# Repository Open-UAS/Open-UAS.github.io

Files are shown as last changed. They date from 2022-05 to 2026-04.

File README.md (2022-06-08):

# [OpenUAS Documentation](https://open-uas.github.io/)

This repository hosts the documentation as a VuePress site. The content can be edited by modifying the .md files and committing the changes.
When pushed to master the website will be recompiled and deployed to https://open-uas.github.io/

See [here](https://open-uas.github.io/Meta_Docs) for details on contributing to this documentation.

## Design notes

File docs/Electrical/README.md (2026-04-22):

# Electrical

Here, you will find details on the electrical system on the current OpenUAS vehicle, including wiring diagrams, recommended components, and device pin-outs.

## Apprentice, 3.0 Wiring Diagram, and 5.0 Wiring Diagram
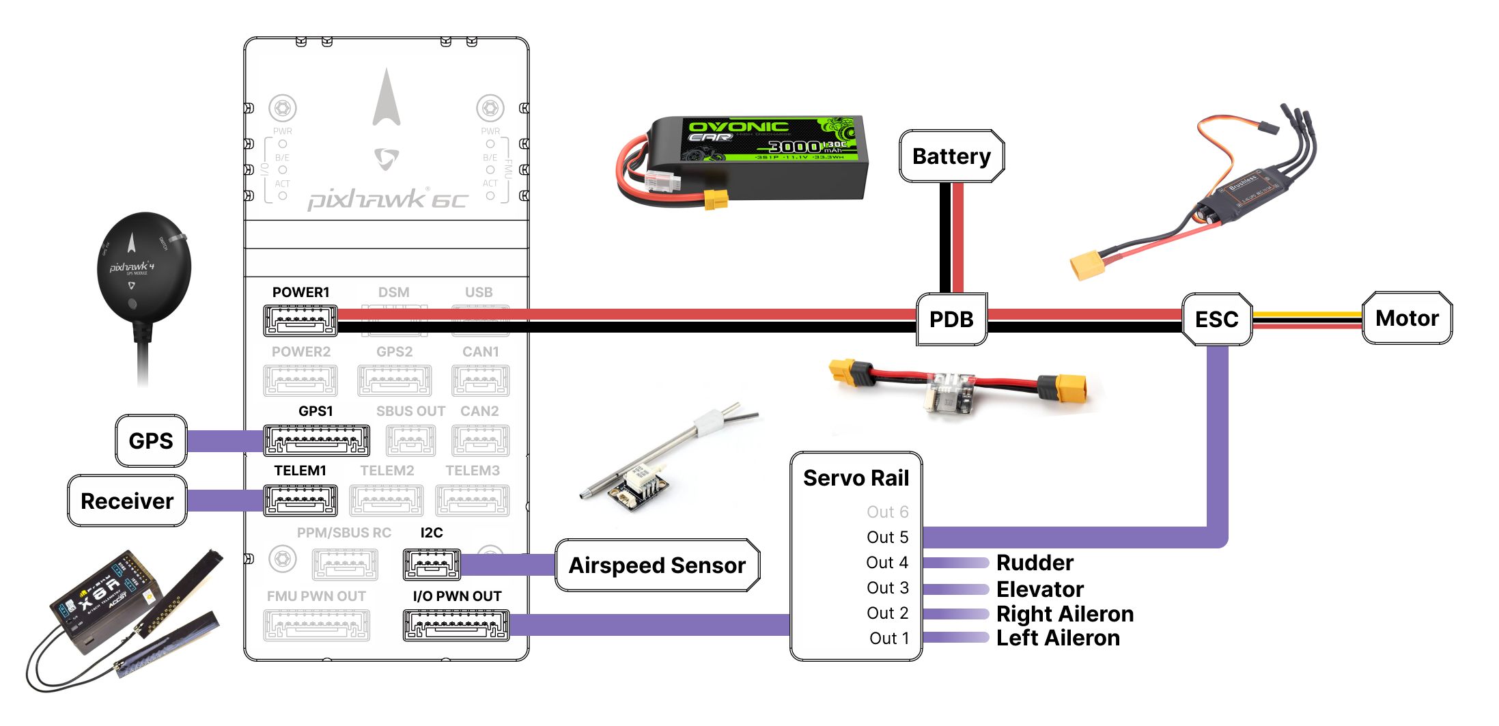
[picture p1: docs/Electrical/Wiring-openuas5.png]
Wiring Diagram Current
 

## PLUMA Wiring Diagram
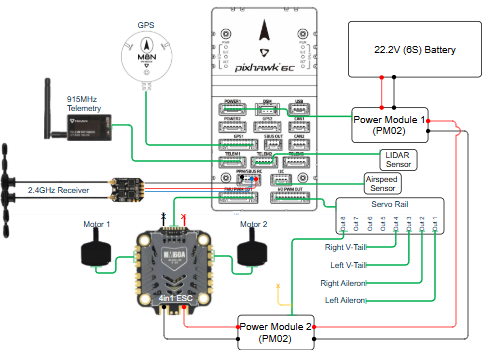
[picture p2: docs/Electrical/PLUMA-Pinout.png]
Wiring Diagram


## Pixhawk 4 Pinout
[Pixhawk 4 Pinout](/Pixhawk4-Pinouts.pdf)
## testing

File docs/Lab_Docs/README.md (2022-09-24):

# Lab Docs
Here you will find general documentation about using tools in the lab or other general documentation.

[iMAX B6 V2 battery charger manual](/manual-iMAXB6AC-v2.pdf)

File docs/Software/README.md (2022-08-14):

# Software

The software solution utilized can be broken up into a few major sections.
* [PX4](PX4.md) Onboard firmware that controls the vehicle and performs autonomous actions.
* [QGroundControl](QGroundControl.md) Ground control software that receives telemetry information commands actions.
* [Simulation](Simulation.md) Software to simulation flight dynamics, used in testing and training.

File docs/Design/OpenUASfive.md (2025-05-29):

# Open UAS 5.0 (work in prog-Karan)
## Summary
The main objective of the OpenUAS 5.0 model is to be affordable and simplistic in materials. The model is designed to serve as a kit with a set of detailed instructions. The 5.0 model is made of a fully 3D printed airframe allowing for more complex geometry with improved aerodynamics The instructions for this model breaks down each step with details, tips, and visuals to aid the reader's process of assembling the model (Still Under Development).

## Goals
- Cost-effective
- Reconfigurable
- Easy to manufacture
- Optimized for research payloads
- 3D printed airframe

## Project Progress:
## CFD Analysis
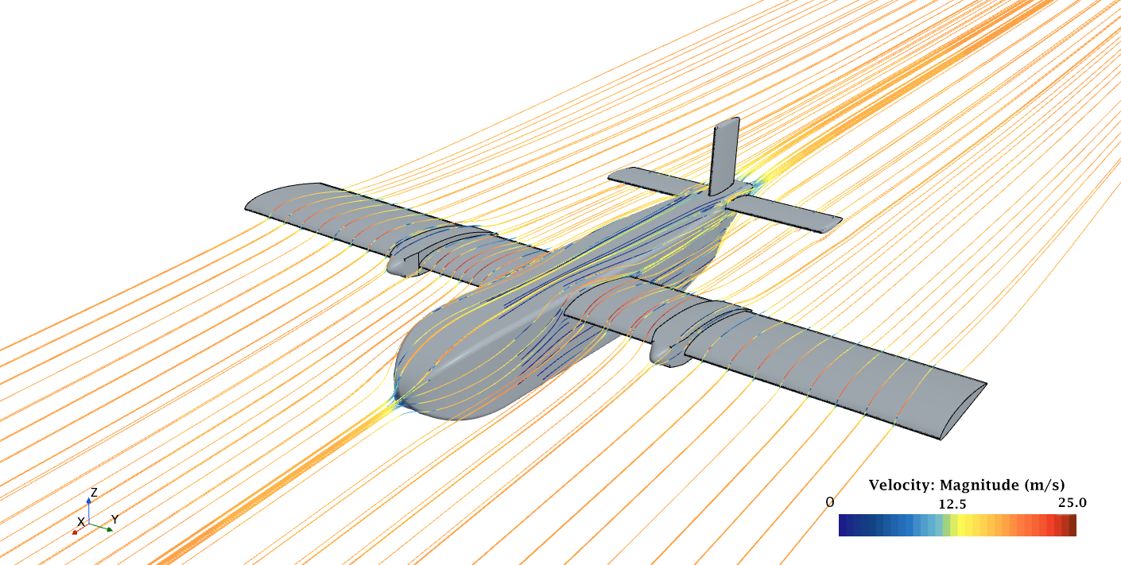
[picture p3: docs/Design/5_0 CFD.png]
OpenUAS 5.0 initial CFD


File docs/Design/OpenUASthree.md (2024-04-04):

# Open UAS 3.0 
## Summary
The main objective of the OpenUAS 3.0 model is to be affordable and simplistic in materials. The model is designed to serve as a kit with a set of detailed instructions. The 3.0 model is largely composed of posterboard and 3D printed materials. The instructions for this model breaks down each step with details, tips, and visuals to aid the reader's process of assembling the model.

## Goals
- Lightweight
- Cost-effective
- Reconfigurable
- Easy to manufacture
- Optimized for electronics

## Solidworks Assembly
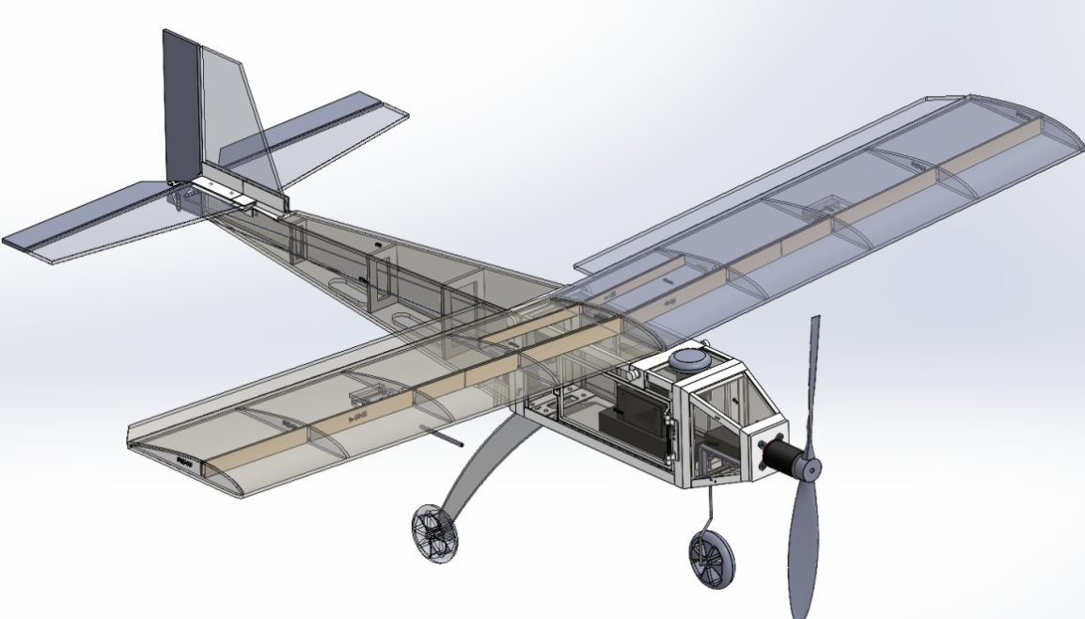
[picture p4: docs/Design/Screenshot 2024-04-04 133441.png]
OpenUAS 3.0 Solidworks


## Model
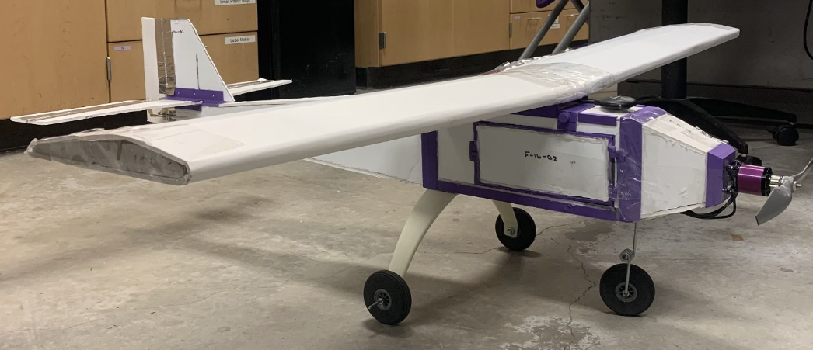
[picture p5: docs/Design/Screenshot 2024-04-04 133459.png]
OpenUAS 3.0 Completed


### Spring 2023 Updates
With this design, we optimized the NACA 2412 airfoil to create the desired aerodynamic characteristics for the wing. By modifying the original NACA 2412, we increased lift and drag slightly.

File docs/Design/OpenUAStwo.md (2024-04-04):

# Open UAS 2.0 
## Summary  
The OpenUAS 2.0 model has a major focus on the use of 3D printed parts to create a framework that can be easily modfided and printed to meet the needs for anyone wanting to use the model. It has an overall weight of 4.07 lbs, keeping it lightweight. It is also adaptable to store more electronics than OpenUAS 1.0 and other UAVs. 

## Requirements: 
- Lightweight
- Cost-effective
- Easy to manufacture
- Optimized for electronics
- Stable during flight

## Solidworks Assembly
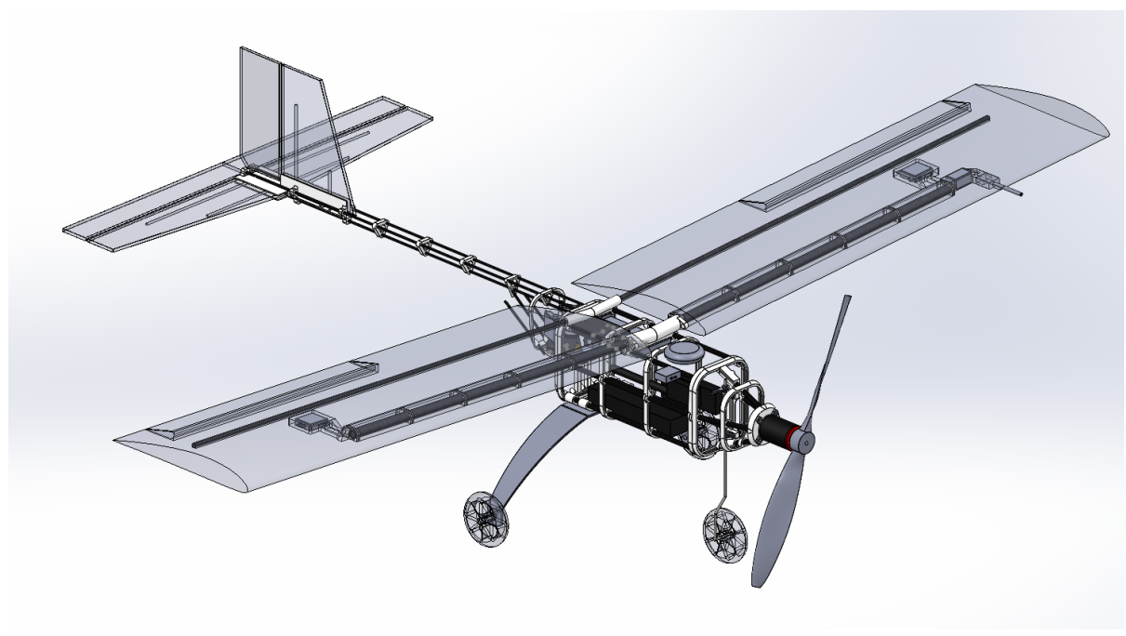
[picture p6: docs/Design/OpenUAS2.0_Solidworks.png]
Solidworks complete


## Model
OpenUAS 2.0 Completed

We will go through some design changes made from Jan 2022-May 2023.

## Spring 2022 Design Changes

There were a few issues that arose with the construction of the 2nd iteration of the OpenUAS project. These were mostly forecasted issues the team had planned mitigation methods for, but  that ended up not working the intended way. There were a few issues that arose that were not foreseen but directly related to the predicted issues. 

## The First Major Area of Issue 
The issues we were faced with all revolved around the tail of the UAS. The original idea was to create a tail that's lightweight and easily replaceable. In order to do this the tail was broken down into a few different parts. These included the carbon fiber support rod, and 3D printed parts including: tail supports, tail feather support, and connection rod of the tail.  

### Twisting of the tail 
The first issue that arose was the amount of twist that appeared in the end of the tail around the tail feather piece. We predicted that there would be a small amount of twist due to using 3 Carbon Fibers rods as the main part of the tail. We believed that it would be negligible, however once the tail was assembled it was clear the twisting was going to be more of an issue then originally predicted.  

One way we attempted to fix this issue was adding more of the tail support pieces in order to add more stiffness along the carbon fiber rods. While this did decrease the amount of twist noticeably, it still did not remove the problem. Other proposed ideas for fixing for the issue was adding a stiffer such as balsa wood or popsicle sticks was taken into consideration however, while working to find a solution the team ran into another issue. 

### Connection between the body and the tail 

Another issue we ran into was not one that we had predicted. When designing the 3D pieces the team created generic ribs that would be used to create the body of the UAS. There were a few assumptions made however when applying the concept of the hinge ribs with the interfacing parts such as the back connection point and the nose cone connection. 

One of the assumptions made was that the 3D printed parts would be printed to a high enough tolerance that connecting with glue while flush with each other would be a quick and easy method of connecting and if needed later removing from each other without having to completely disassemble the body or tail parts. This proved to not be the case when the time came to connect the two parts. 

One thing that had been overlooked with the 3D printed parts was the flexibility of the pieces. ABS was the material used to print the ribs and the connection piece and while the material considered relatively stiff for our needs the material is still able to bend or warp without losing its shape if a force applied to it. When we went to attach the parts together, we clamped the two of them together; it became hard to hold them together while the glue set and the final product was not within the desired tolerance of connection. Instead of a solid connection we had half of the connection bowing outwards towards the end of the tail instead of inwards toward the body like we had planned. 

The issue was made worse when the control surfaces were added to the tail feather and it was clear the added weight was making the problem worse. Much like the twisting problem we had a number of proposed ideas in order to correct the issue. Looking at table 1.

### Table 1
Solution | How it would fix the problem | Why we went with it or not | Was it the final solution we picked? |
|:----:|:---------------------------------------------------------------|:--------------------------------------------------------------------------|:---------:|
| Elastic bands | The elastic bands would be fastened to the top of the tail piece and then would be wrapped and unwrapped around a part connected to the body of the UAS when accessing the electronics. | After creating a mock-up setup of the idea using string we determined that the flexibility of the ABS material was keeping us from properly tensioning the string and would not be a great solution to the issue. | No |
| Velcro | The top surface of the body and the tail connection piece are meant to be flush when assembled. In order to keep the tail piece from bowing backwards velcro would be placed along the top of the back rib and the connection tailpiece. When we need access to the electronics and interior of the UAS the top piece of velcro would be removed in order to allow the hinge to work correctly. | When we tested the idea by placing velcro pieces on the surface it was seen that the bowing still occurred. Not only that but when moving the UAS the velcro came loose and was not effective.  | No |
| Rod method 1 | This method would include attaching another carbon fiber rod at the base of the body and the end of the tail feather diagonally to force the tail piece upwards. | This method would have been hard to add to the current design as is and runs the risk of breaking during rough landings. | No |
| Rod method 2 | Similar to the 1st rod method the 2nd would involve adding a new rod. A big difference in the method would be removing the 3 smaller carbon fiber rods and replacing them with one large rod that would run from the nose cone to the end of the tail.Instead of adding the diagonal support from the body to the tail. | Like the first rod method we would have to re-design the 3D printed parts. In this case we decided that this approach would be effective in fixing the issue in the smallest amount of time and amount of labor. It would also result in fixing the issue with the twist of the tail feather. | Yes |

## Our solution to the First Issue 
After mocking up and reviewing different ideas between the sub-teams we determined that using the 2nd rod method would be our best course of action. This was based on the fact the rod would not only fix the issue with the bowing but it would also address the twisting problem in the tail at the same time. 

We were not able to mock up this idea in our lab space however, we were able to compare the stiffness from the assembled tail and the singular rod we would add. We did this by applying a small amount of force on each of the structures to determine how much bending would occur. (should we measure the amount of bending for quantitative data(plus another table would be cool))
Once we determined that the singular rod would be the best solution to reduce the bowing in the part we took a look at the twisting. In order to incorporate the rod we had to redesign the tail feather and connection parts. Our theory is that by taking the time to redesign the tail feather we can reduce the twisting at the end of the tail. Primary because the bowing and bending of the 3 carbon fiber rods will no longer be a problem when the tail is one solid rod along the length of the UAS’s body and tail.

## Second Area of Issue 

After the assmebly of the new tail was completed we came across another issue with the 2.0 model. The issue this time instead of being around the tail was the on the body/fuselogde of the model. This model includes the use of neodynimum magnets inorder to keep the clam shell design closed during however, it was discovered that the smaller magnets were not strong enough to hold the shell closed under minor turbulance. 

### Table 2 
Solution | How it would fix the problem | Why we went with it or not | Was it the final solution we picked? |
|:----:|:---------------------------------------------------------------|:--------------------------------------------------------------------------|:---------:|
| Velcro| The Velcro would be able to hold the two halfs closed during flight| We chose not to go with this soultion as there was not enough surface area for the velcro to be affective. | No |
| Zip Ties | Zip Ties is somthing we chose to use as a short term solution in order to close the clam shell | long term the soultion this is not sustanble as the zip ties would have to be cut and a new one to replace them each time we wanted access to the electronics | No |
| 3D Printed Part | A 3D printed part would be more of an insert piece that would screwed together in order to keep the two halfs closed | This was our chosen soultion as it would not add a lot to the system and would a good fit for the part | Yes |

# Spring 2023 Changes 

The changes made during this round were needed for fine tuning of components for the function of the model instead of fixing dramic issues with model like previous changes.  

## Motor Mount Adjustment

After some observions of other air crafts we noticed that the motors for the propeller may benfit from an angled motor instead of a completly straight faceing. We angled our motor to the right and directed down of the model. In order to do this we added nuts to the motor bolts to create the spacing for the angle. This inculded four mounting points and a total of 5 nuts. Two of the nuts were placed on the upper right corner and the upper left corner. 

## Test Flight
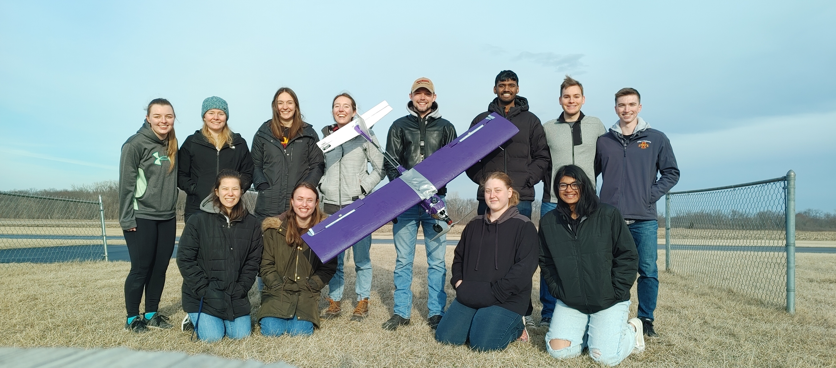
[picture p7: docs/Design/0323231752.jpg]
OpenUAS 2.0 Flight Test


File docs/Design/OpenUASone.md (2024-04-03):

# Open UAS 1.0 

A carbon fiber edtion of the OpenUAS project, built in 2020.
#
OpenUAS1.0 Full Design

More information can be found on the [Laboratory for Temporal Logic Youtube Page](https://www.youtube.com/watch?v=xZF81fSSzbI).
### Requirements include:

1. Configurable: Wings can be changed
2. Can break down and moved easily
3. Simple assembly
4. Does not require a runway
5. Can be manufactured by hobbyist
6. Can withstand a crash landing

### Design Goals
Development for design goals began in 2019.

Overall weight: 4.138 lbs

### Lessons Learned
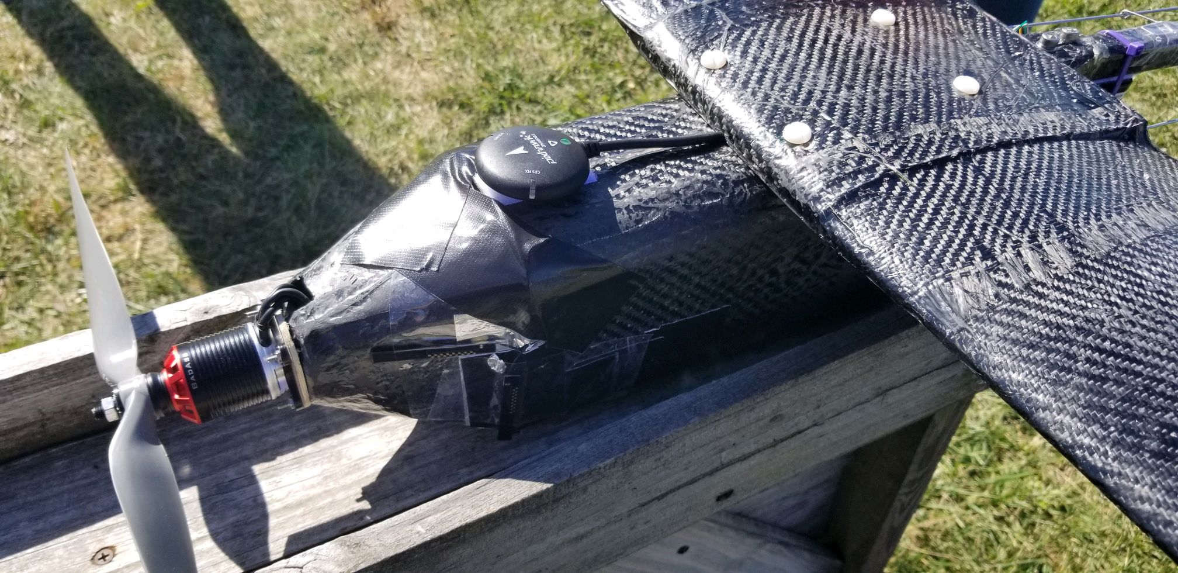
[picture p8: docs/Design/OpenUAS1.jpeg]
OpenUAS 1.0 Completed
\
The next iteration must have the following capabilities:
- Better access to electronics
- Better flight characteristics
- Better reparability
- Tailwheel configuration is harder to control
- Better Manufacturability
- Better transportability (multiple piece wing)
- Better corrective action for left turning tendencies

### Team 
Team Members from left to right: Will Burken, John Edgren, Ellie Diersen, Marcella Anderson, Colton Glick, John Levandowski (not pictured), Christopher Johannsen (not pictured), Stephanie Jou (not pictured)
#
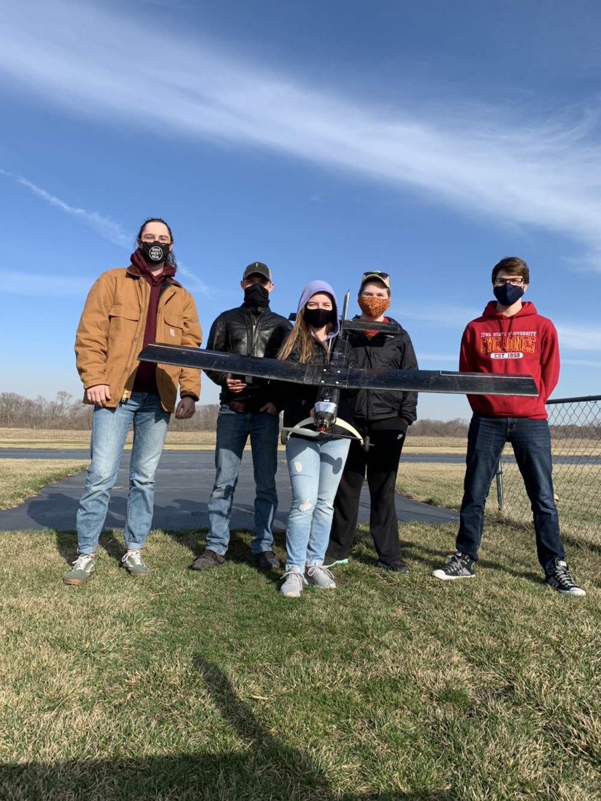
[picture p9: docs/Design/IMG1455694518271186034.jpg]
OpenUAS 1.0 Team


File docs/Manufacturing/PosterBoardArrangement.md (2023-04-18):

# Poster Board Arrangement Settings  
Poster boards can be used to manufacture some parts of the fuselage and wing. It's important to find the best arrangement of these parts to reduce material waste. This problem is generally referred to as the bin packing problem. Several algorithms have been developed to solve this problem before with JS, MATLAB, and C++. Based on our research, the libnest2d library is the easiest, most effective algorithm for finding the best arrangement to cut parts on the poster board. To ease the process, PrusaSlicer 2.5.0 can be downloaded since the libnest2d library is already integrated within this open-source 3D printing software.  
 
References:<br> 
[Bin Packing Problem](https://en.wikipedia.org/wiki/Bin_packing_problem)<br>
[Libnest2d Library](https://github.com/tamasmeszaros/libnest2d)<br>
[PrusaSlicer Download](https://www.prusa3d.com/page/prusaslicer_424/)
 
## 1. Create STL Files 
First, to use the PursaSlicer, you will need to create STL files of your parts using CAD software such as Fusion360 or SolidWorks. If you are using Fusion360, you can export the parts as STL files by right-clicking on the body and selecting 'Save as Mesh'. Even if your parts are designed in other units, you must choose the mm units from the 'Save as Mesh' options. If you are using SolidWorks, you can go to File -> Save As and select the document type as STL. Then, click on the 'Options' button and convert the units to mm. PrusaSlicer software doesn't have the option to change the global units. If STL files are exported with inch units, you can scale the parts by 2540%. It's important to note that the thickness of your parts must be the same as the thickness of the material that will be used.  
 
## 2. Import to PrusaSlicer 
After opening the PrusaSlicer, set the bed dimensions to the same size as your material board in mm units from Printer Settings -> Bed Shape -> Settings -> Size. Then head back to the Plater page, and you can import as many parts as possible  
from File -> Import or using the Ctrl + I shortcut. 
 
## 3. Arrange (Bin Packing Problem) 
The imported parts can be in different orientations. Rotate each part until they are all parallel to the bed. Select the required spacing between parts and check to enable the rotations option by right-clicking on the arrange option at the toolbox bar on the upper side of the window. Then you can check for different alignment options with shortcut A. If you are cutting the parts with CNC for better machining, make sure the spacing is at least the same as the tolerance of your machine. If you are cutting the parts with a knife, we recommend setting the spacing to 1 mm.   
 
## 4.1 Export (For Machining) 
If your machine works with G-code, you can easily export the G-code with Ctrl + G shortcut. If STEP, DWG, or DXF formats are needed, we recommend exporting the plate as an STL file and then post-processing it in Fusion360 or SolidWorks with relevant manufacturing settings. 
 
## 4.2 Export (For Cutting with Knife) 
 
<u>1. via Fusion360</u>
 
After exporting the plate as an STL file, open it via Fusion360. Go to  
Design Workspace -> Mesh -> Modify -> Convert Mesh and select all the meshes to convert them to bodies. Now, you can see the coordinates of your parts on the bottom right of the window by clicking on the corner points of the parts. If the origin is not the same as the bed origin in PrusaSlicer, go to Manufacture Workspace -> Fabrication -> Setup. Set operation type as cutting and orientation as select X & Y axes. Select the X and Y axis from the corner of the reference region manually (Red: x-axis / Green: y-axis) and then set the origin setting to the selected point. 
 
<u>2. via SolidWorks</u>

Go to File -> Open and select the STL file. Then, click on the 'Options' button and select the surface body from the 'import as' option. You can see the coordinates of your parts on the bottom right of the window by clicking on the corner points of the parts.  
 
You can mark these locations on the posterboard and connect the dots to create the part drawings to cut them with a utility knife. We recommend holding a metal straight edge flush with the edge you are cutting and running the knife along the metal.  

Here is the poster board arrangement (22x28-in) we created following the procedures above.

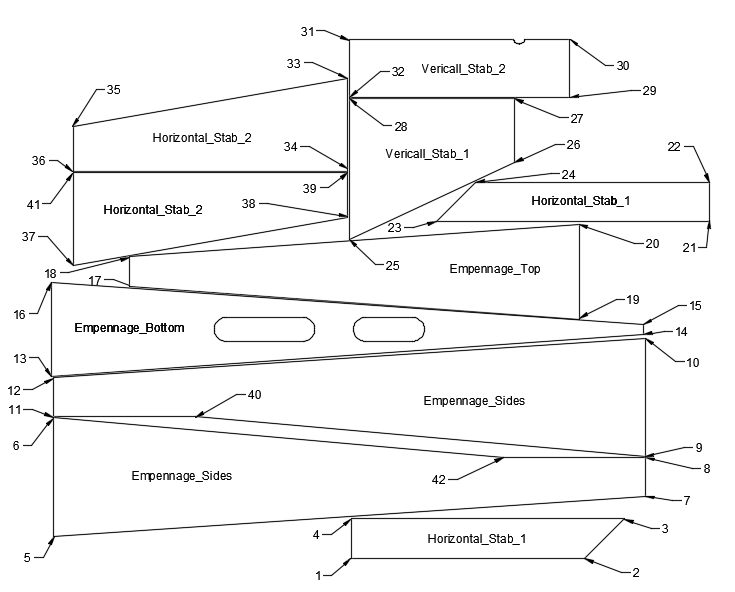
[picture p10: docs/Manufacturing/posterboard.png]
Poster Board


| # | x-axis | y-axis | # | x-axis | y-axis | # | x-axis | y-axis | # | x-axis | y-axis |
|---|---|---|---|---|---|---|---|---|---|---|---|
| 1 | 323.848  | 0.254 | 12 | 4.561 | 194.502  | 23 | 415.121  | 361.505  | 34 | 320.514 | 415.991 |
| 2 | 574.673  | 0.254 | 13 | 2.497 | 195.357  | 24 | 457.624  | 404.008  | 35 | 25.747 | 463.784 |
| 3 | 617.176  | 42.757 | 14 | 637.497  | 241.077  | 25 | 322.022  | 342.299  | 36 | 25.747 | 415.991 |
| 4 | 323.848  | 42.757 | 15 | 637.497  | 251.237  | 26 | 499.314  | 424.971  | 37 | 25.747 | 314.709 |
| 5 | 4.651 | 24.167 | 16 | 2.497 | 296.957  | 27 | 499.314  | 494.046  | 38 | 320.514 | 366.69 |
| 6 | 4.651 | 151.167  | 17 | 86.038 | 291.945  | 28 | 322.022  | 494.046  | 39 | 320.514 | 414.483 |
| 7 | 639.561  | 66.5 | 18 | 86.038 | 324.05 | 29 | 558.75 | 495.3 | 40 | 156.961 | 152.169 |
| 8 | 639.561  | 108.833  | 19 | 568.638  | 257.197  | 30 | 558.75 | 557.213  | 41 | 25.747 | 414.483 |
| 9 | 639.561  | 109.835  | 20 | 568.638  | 358.798  | 31 | 321.768  | 557.213  | 42 | 487.161 | 108.833 |
| 10 | 639.561  | 236.835  | 21 | 708.449  | 361.505  | 32 | 321.768  | 495.3 | 43 | | |
| 11 | 4.561 | 152.169  | 22 | 708.449  | 404.008  | 33 | 320.514  | 515.764  | 44 | | |

X and Y coordinates are in mm units.

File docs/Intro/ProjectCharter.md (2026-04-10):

# Project Charter

## Project Name
OpenUAS

## Principal Investigator
Dr. Kristin Y. Rozier

## Project Team
- Artur Nunes
- Mukul Kulkarni
- Broderick Urbanz
- Grant Goebel
- Tyler Kazmarski
- Gustavo Luzzi
- Sam McClure
- Grace Gilsdorf
- Aidan Sippel
- Karanvir Singh
- Akwasi Quarcoo
- Saira Farooz
- Anderson Keough
- Abhigyaan Deep 
- Maria Zambrano Sanchez
- Fionna Schaack
- Shersta Anupindi

## Revisions
* **Revision:** E
* **Rev Date:** 05/26/2025
* **Originally Dated:** 09/20/2017

## Background
No open-source UAS options exist that are fixed-wing and accessible (conceptually) to the general public. Some similar, available UAS’ are the Albatross (created and sold commercially by Applied Aeronautics) and Razor (created a UVA). Open source software options already available include ArduPilot and PX4.

## Project Scope
We are producing an open-source, COTS UAS that can be used for education and research purposes; the UAS shall only consist of components available to the general public. 

## Project Objectives
* Create an open-source, COTS UAS for educational and research flights
* Provide full documentation of the conception, design, and testing of all systems
* Act as a test bed for Dr. Rozier's system health management experiments
* Be easily launched and not require a runway for takeoff or landing
* Be piloted by students and hobbyists
* Be reconfigurable and support additional components

## Project Deliverables
* A functioning design and prototype of a UAS
* Relevant tools for piloting the UAS from the ground
* Extensive documentation of the design process
* Extensive documentation of the manufacturing process
* Extensive documentation on proper use and safety

## Project Constraints
* COTS components
* Affordable components
* Easily duplicated components (e.g. all 3D printed parts can be reasonably produced by hobbyists)
* All components should be reasonably safe (e.g. battery)
* Documentation and design must allow for construction by non-specialists

## Project Assumptions
* The UAS shall be fixed-wing
* The UAS can be constructed in a maker space
* There is a customizable autopilot available
* There is existing hardware, material, and design technology available
* The UAS can be built by someone with a minimum of a high school education

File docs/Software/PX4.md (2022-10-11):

# PX4

PX4 autopilot is the main software stack that controls the UAS. It has been forked to the [OpenUAS repo](https://github.com/Open-UAS/PX4-Autopilot) to allow our own custom modifications. The upstream repo can be viewed at, [github.com/PX4/PX4-Autopilot](https://github.com/PX4/PX4-Autopilot)

PX4 allows for many out of the box capabilities such as flight stabilization, automatic flight paths, and automatic take off. Further details about PX4's features can be found in the [PX4 documentation](https://docs.px4.io/main/en/)

## Dev Environment Setup
This setup can get fairly complicated with all the dependencies that PX4 requires. A new method that alleviates some of this is using a docker container to compile PX4. This pre-packages the dependencies required to build PX4

### Using the Docker Toolchain (Recommended)

**Windows with WSL 2**
1. Be sure virtualization is enabled on your machine through the bios.
2. Install Windows Subsystem for Linux 2 (WSL 2) by opening an *administrator* command prompt and running `wsl --install --distribution Ubuntu-20.04`
3. Reboot your machine 
4. Install Docker engine through WSL2, [Docker Engine, Ubuntu install](https://docs.docker.com/engine/install/ubuntu/)
5. Do [Docker post install steps](https://docs.docker.com/engine/install/linux-postinstall/) to run docker as non-root.
6. Once your development tools are all setup, go ahead and use git to clone the OpenUAS PX4-autopilot repository from [https://github.com/Open-UAS/PX4-Autopilot](https://github.com/Open-UAS/PX4-Autopilot) and checkout the stable branch.

**Linux**
1. Install Docker engine, [Docker Engine, Ubuntu install](https://docs.docker.com/engine/install/ubuntu/)
2. Do [Docker post install steps](https://docs.docker.com/engine/install/linux-postinstall/) to run docker as non-root.
3. Once your development tools are all setup, go ahead and clone the OpenUAS PX4-autopilot repository from [https://github.com/Open-UAS/PX4-Autopilot](https://github.com/Open-UAS/PX4-Autopilot) and checkout the stable branch.

### Without Docker

**Windows with WSL 2**
1. Install Windows Subsystem for Linux 2 (WSL 2) by opening an *administrator* command prompt and running `wsl --install --distribution Ubuntu-20.04`
2. Reboot your machine 
3. Once your development tools are all setup, go ahead and clone the OpenUAS PX4-autopilot repository from [https://github.com/Open-UAS/PX4-Autopilot](https://github.com/Open-UAS/PX4-Autopilot) and checkout the stable branch.

**Ubuntu 18.04/20.04 Native/Virtual Machine**

Note from the PX4 User Guide:

The supported OS versions for PX4 development are Ubuntu Linux LTS 18.04 (Bionic Beaver) and 20.04 (Focal Fossa).

1. Clone forked px4 repository to your machine `git clone --branch stable https://github.com/LTL-AERO/PX4-Autopilot.git`
2. Move into the newly cloned px4 repository `cd PX4-Autopilot`
3. Run `git submodule update --init --recursive` to clone all submodules within the repository, to your machine
     - alternatively `git submodule update --init --recursive <submodule folder>` can be used if you know the specific submodule needed 
     - `git submodule update --recursive` can be run in the future to update all submodules
4. Setup development environment and install dependencies, more information about development environment setup can be found here: [https://dev.px4.io/master/en/setup/dev_env_linux.html](https://dev.px4.io/master/en/setup/dev_env_linux.html)
     - Run the ubuntu.sh to install the required dependencies(including gazebo for simulation) then reboot:`bash ./Tools/setup/ubuntu.sh`
5. Done.
      - [Steps for building PX4 firmware](#building-on-ubuntu-18-04-20-04-native-virtual-machine)
      - [Steps for running Gazebo](Simulation.md#without-docker)

**Native Windows**
:::warning
This configuration will not be able to run the gazebo simulation.
Gazebo is a Linux only software so it must be run through WSL or natively on Linux.
:::
- Details on this configuration may be lacking as not many people have used it before. 
- Check the PX4 docs for this configuration [https://docs.px4.io/main/en/dev_setup/dev_env_windows_cygwin.html](https://docs.px4.io/main/en/dev_setup/dev_env_windows_cygwin.html)

## Building and Flashing Custom Firmware
See [Dev Environment Setup](#dev-environment-setup) for setup details.

### Building with Docker (Recommended)
1. Open a linux terminal to the root of the PX4 folder structure.
2. Be sure the docker daemon is running by running `sudo service docker start` or `sudo systemctl start docker` depending on if your distro uses SysVinit or Systemd.
3. Run `./Tools/docker_run.sh make px4_fmu-v5_default`. This will start a new docker container and compile the firmware for Pixhawk 4.
    - If you get compilation errors, it can be a good idea to run `./Tools/docker_run.sh make clean` to put the build process in a clean state
    - Using the docker build script follows this format, `./Tools/docker_run.sh {command to execute}`
        - `./Tools/docker_run.sh bash` can be run to look around in the docker container file system 
    - See [Building PX4](https://docs.px4.io/main/en/dev_setup/building_px4.html#nuttx-pixhawk-based-boards) for all available targets
4. Once compilation is complete the firmware will be under the `build` folder as `px4_fmu-v5_default.px4` among other files.

### Building on Ubuntu 18.04/20.04 Native/Virtual Machine 
- Open a linux terminal to the root of the PX4 folder structure.
- Run `make px4_fmu-v5_default`.
    - If you get compilation errors, it can be a good idea to run `make clean` to put the build process in a clean state
    - See [Building PX4](https://docs.px4.io/main/en/dev_setup/building_px4.html) for all available targets
- Once compilation is complete the firmware will be under the `build` folder as `px4_fmu-v5_default.px4` among other files.

### Flash Firmware With QGroundControl
- Open QGC and go to vehicle setup, then firmware tab.
- Plug the Pixhawk 4 into your machine via USB, it should auto detect and QGC will prompt you what firmware to flash.
- Select advanced settings, and set the custom firmware file option in the version drop down.
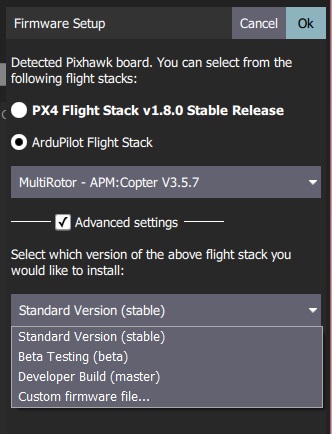
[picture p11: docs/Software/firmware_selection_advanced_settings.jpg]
Advanced settings

- Select our newly created `PX4_fmu-v5_default.px4` file and click ok to start flashing.
- Wait for the Pixhawk to reboot to complete the update.

## Custom Airframes

Within PX4 there are definitions called [airframes](https://docs.px4.io/main/en/dev_airframes/#airframes). These definitions control things like, number of control surfaces, propeller configurations, and vehicle parameters among other settings. PX4 comes [pre-loaded](https://docs.px4.io/main/en/airframes/airframe_reference.html) with many airframes, but we can add our own custom airframes to support configuration and modification efforts. 

The PX4 docs have a great step by step guide for adding a new airframe [here](https://docs.px4.io/main/en/dev_airframes/adding_a_new_frame.html).

In this documentation we will cover what has been added to stock PX4 to get the new airframes setup.

### OpenUAS Airframe (2150)

This airframe is intended for the current OpenUAS vehicle and should be adapted and modified as the physical design changes.

- Created new config file in [ROMFS/px4fmu_common/init.d/airframes](https://github.com/Open-UAS/PX4-Autopilot/blob/stable/ROMFS/px4fmu_common/init.d/airframes/2150_open_uas) and [ROMFS/px4fmu_common/init.d-posix/airframes](https://github.com/Open-UAS/PX4-Autopilot/blob/stable/ROMFS/px4fmu_common/init.d-posix/airframes/2150_open_uas) (the posix folder is used by the gazebo simulation while the non-posix folder is used by the Pixhawk. The config files' content should be identical) with the autostart id prepended to the filename.
-  Added the new config file to the airframe CMakeLists.txt file in each folder, [ROMFS/init.d/airframes/CMakeLists.txt](https://github.com/Open-UAS/PX4-Autopilot/blob/stable/ROMFS/px4fmu_common/init.d/airframes/CMakeLists.txt#L47) and [ROMFS/init.d-posix/airframes/CMakeLists.txt](https://github.com/Open-UAS/PX4-Autopilot/blob/stable/ROMFS/px4fmu_common/init.d-posix/airframes/CMakeLists.txt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)
- Added OpenUAS mixer to [/ROMFS/px4mu_common/mixers/](https://github.com/Open-UAS/PX4-Autopilot/blob/stable/ROMFS/px4fmu_common/mixers/open_uas_apprentice.main.mix)
    - Which mixer to use is set in the airframe config file created earlier.
    - [See below](#openuas-mixer) for more details on mixers. 

See [Using The OpenUAS Airframe](./QGroundControl.md#using-the-openuas-airframe) for details and enabling the new airframe in QGC.

### Apprentice Airframe (2151)

This airframe is intended to run on the Apprentice aircraft that we utilize for other development tasks. This airframe was not utilized as much as the other so may not be up to date. 

A similar approach was taken to add this custom airframe as previous.

- Add the new config file to [ROMFS/px4fmu_common/init.d/airframes/](https://github.com/Open-UAS/PX4-Autopilot/blob/stable/ROMFS/px4fmu_common/init.d/airframes/2151_open_uas_apprentice)
- Add the config file to the [CMakeLists.txt](https://github.com/Open-UAS/PX4-Autopilot/blob/stable/ROMFS/px4fmu_common/init.d/airframes/CMakeLists.txt#L48) file

## OpenUAS Mixer
[Mixers](https://docs.px4.io/main/en/concept/mixing.html) are used to take commands (roll, pitch, yaw, throttle) from the PX4 system and map those commands to actuator outputs, including servo mapping, min and max values, and direction. This is preferable to mapping the outputs with the RC controller because the autopilot will utilize the mixer and not the RC controller mappings. Meaning the trims, and servo mappings can be applied system wide.

The mixer for the custom airframes are defined in the `ROMFS/px4fmu_common/mixers` folder eg [open_uas_apprentice.main.mix](https://github.com/Open-UAS/PX4-Autopilot/blob/stable/ROMFS/px4fmu_common/mixers/open_uas_apprentice.main.mix) . The mixer files can get somewhat confusing to understand, details on writing mixers can be found on the [PX4 docs](https://docs.px4.io/main/en/concept/mixing.html#px4-mixer-definitions). The general idea is that you have n number of actuator outputs, each of those n actuators are defined to be driven by 1 or more outputs from PX4. The mixer file is defined sequentially, starting with actuator 1, then 2, 3 ... to n actuators. These actuator numbers correspond to the pwm port number on the [Pixhawk wiring](http://localhost:8080/Electrical/#current-wiring-diagram). 

The default mixer file can be **overridden** at runtime by placing the mix file with the same name (eg `open_uas_apprentice.main.mix`) onto the Pixhawk SD card under `/etc/mixers/` This mix file will be loaded instead of the default one defined at compile time.

## Parameters and Configuration
PX4 allows the user to control the behavior of the autopilot through hundreds of parameters. This is the main way that we customize the OpenUAS and control its behavior. 

The current parameters of the connected vehicle set can always be viewed in [QGroundControl](./QGroundControl.md) under vehicle setup > parameters.
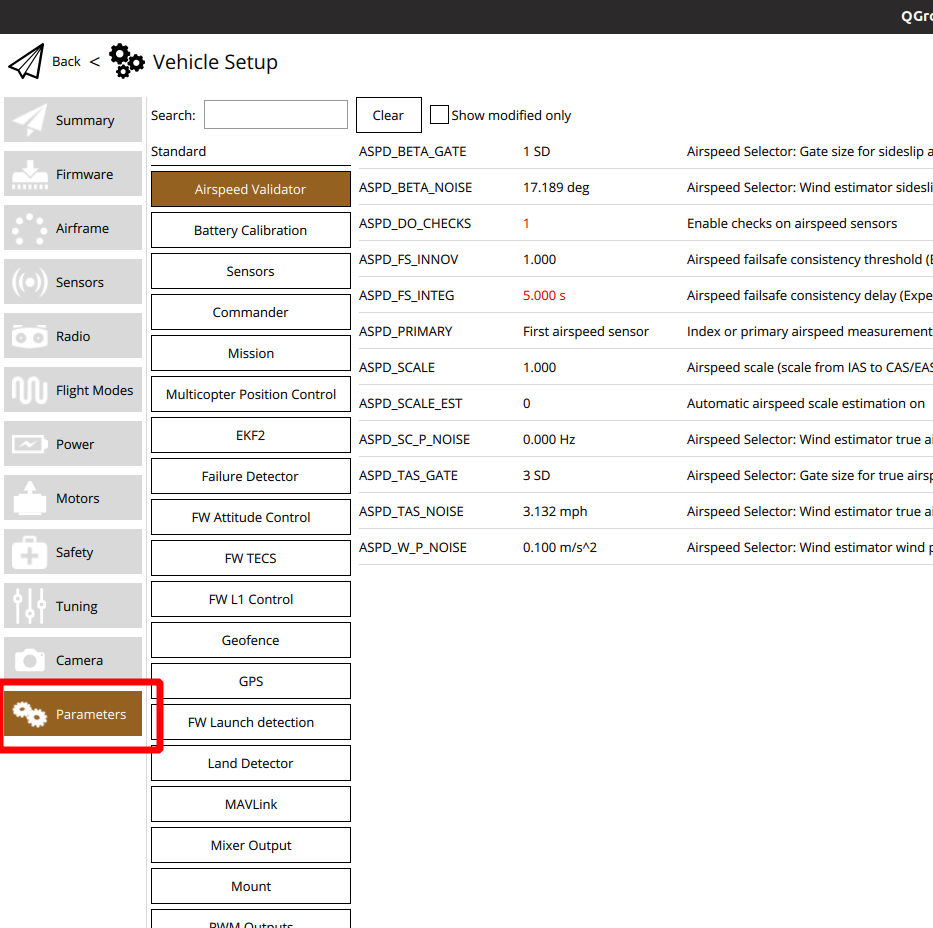
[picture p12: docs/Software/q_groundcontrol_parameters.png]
Parameters


Some parameters are initialized by the airframe definition file, ex: [PX4-Autopilot/ROMFS/px4fmu_common/init.d/airframes/2150_open_uas](https://github.com/Open-UAS/PX4-Autopilot/blob/stable/ROMFS/px4fmu_common/init.d/airframes/2150_open_uas) and some parameters are modified later by the user. Because of this, all modified parameters are reset when switching to a new airframe, but parameters are saved if the vehicle is simply powered off.

### Important Parameters

PX4 includes hundreds of parameters to modify, a full list of all available parameters can be found in the [PX4 docs](https://docs.px4.io/main/en/advanced_config/parameter_reference.html). Below are some parameters of note that we have modified in the past.

#### BAT1_CAPACITY
Specifies the capacity of the battery in mAh. Needed for accurate battery percentage readings.

#### BAT1_N_CELLS
Specifies the number of cells our battery has (we normally use 3S batteries). Needed for an accurate voltage measurement of the battery.

#### BAT1_V_CHARGED
Specifies the charged voltage of one cell of the battery. Needed for accurate battery percentage readings. This value is typically around 4.2V (12.6V total battery voltage when fully charged)

#### BAT1_V_EMPTY
Specifies the voltage to classify a battery cell as empty. Needed for accurate battery percentage readings. A safe value would be around 3.5V (giving total battery voltage of 10.5 when empty). Can use more of the battery by setting this value to around 3V (9v total battery voltage when empty). DO NOT set this value lower than 2.8V.

#### BAT1_R_INTERNAL
Specifies the internal resistance of the battery in ohms. Optionally needed to improve the battery percentage readings and current draw readings. This value can be measured using the battery charger we have in the lab. A typical value is around 0.006 ohms.

#### COM_ARM_WO_GPS
Allows for PX4 to be armed without a GPS signal. This is required to arm the OpenUAS in the basement of Howe where no GPS signal can be acquired.

#### COM_DISARM_LAND
Specifies the amount of time after landing to automatically disarm the vehicle. If set to 0s, does not disarm on landing. This parameter is intended more for quad-copters than fixed wing planes. We typically set this value to 0 to not disarm on landing.

#### COM_DISARM_PRFLT
Specifies the amount of time after arming which if not taken off, will automatically disarm the vehicle. If set to 0s, does not disarm. We typically set this value to 0 to not disarm when trying to takeoff.

#### FW_FLAPS_SCL
Specifies a scale factor for the flaps. If set to 100% the flaps will move the ailerons to the their max travel when flaps are deployed, 50% will move them half of their travel.

#### FW_LND_EARLYCFG 
When true, sets the flaps position during the final loiter loop of the automatic landing sequence instead of on the final approach. Typically set to true.

#### FW_P_LIM_MAX and FW_P_LIM_MIN
Specifies the min and max pitch angles the controller will command the vehicle to achieve. This is only in effect in autonomous modes, including altitude and position control flight mode.

#### FW_R_LIM
Specifies the max roll angle the controller will command the vehicle to achieve. This is only in effect in autonomous modes, including altitude and position control flight mode.

#### LAUN_ALL_ON
Turns on launch detection to launch the vehicle with a catapult launch or with a hand launch

#### LAUN_CAT_A
Specifies the acceleration threshold to detect a launch event.

#### LAUN_CAT_T
Specifies the required time an acceleration must be held for to detect a launch event.

#### NAV_ACC_RAD
Specifies the acceptance radius of hitting a waypoint in autonomous flight.

#### PWM_MAIN_TRIM0
Trims the center point of the servo number at the end of the parameter name. Needed to center each servo before flight.

#### PWM_MAIN_REV0
Reverses the direction of the server number at the end of the parameter name.

#### RWTO_TKOFF
Specifies we are taking off on a runway with landing gear. Used for automatic takeoff.

#### SENS_EN_SF0X
Sets what LightWare sensor is in use for the *serial port*, normally set to SF11/c.

#### SENS_SF0X_CFG
Sets what *serial port* the LightWare distance sensor is plugged into. Normally set to TELEM2.

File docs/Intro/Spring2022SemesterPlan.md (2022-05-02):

# OpenUAS
  
# Semester Plan of Work

| Semester Week Beginning | Major Objectives |
| --- | --- |
| 01/17 | |
| 01/24 | |
| 01/31 | | 
| 02/07 | Develop new position advertisements |
| 02/14 | Send out new member applications | 
| 02/21 |  | 
| 02/28 | Host interviews, preliminary design review, Test flight time frame | 
| 03/07 | Host interviews, first draft of documentation due | 
| 03/14 | Spring Break |
| 03/21 | Review documentation, send out acceptance letters | 
| 03/28 |  |
| 04/04 | Onboard new students |
| 04/11 | Final Draft of documentation due | 
| 04/18 | New flight model to be finalized | 
| 04/25 | Order parts for new model (reduces strain on next semester) |
| 05/02 | Ensure documentation is wrapped up and ready to go |

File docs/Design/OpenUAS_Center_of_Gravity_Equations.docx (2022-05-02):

VARIABLES USED:

M_N | Moment about nose
W | Weight of individual component
d | Moment arm
cg1 | Center of gravity without wings/fuel
c | Mean chord length
S | Wing planform area
b | Wingspan
mac | Mean aerodynamic center
cgw | Wing center of gravity
cg2 | Center of gravity with wings and fuel added
M_(N,all) | Moment including wings/fuel
W_(wing+fuel) | Weight of wings plus fuel
l_(HT) | Moment arm from center of gravity to aerodynamic center of gravity of horizontal tail
cght | Aerodynamic center of gravity of horizontal tail
l_(VT) | Moment arm from center of gravity to aerodynamic center of gravity of vertical tail
cgvt | Aerodynamic center of gravity of vertical tail
S_(HT) | Planform area of horizontal tail
V_(HT) | Horizontal tail volume
S_(VT) | Sideview area of vertical tail
V_(VT) | Vertical tail volume
x_n | Neutral point
sm | Static margin
(x_(ac) )_(wing) | Longitudinal position of the wing aerodynamic center

MAIN EQUATIONS USED:

Eq.1 – Moment about nose

M_N =W*d

Eq.2 – Center of gravity without wings/fuel

cg1= (∑ M_N)/W

Eq.3 – Mean chord length

c= S/b

Eq.4 – Mean aerodynamic center of wing

mac =0.25c

Eq.5 – Wing center of gravity

cgw=0.4c

Eq.6 – Center of gravity adjusted for wing and fuel

cg2= (∑ M_(N,all))/(W+W_(wing+fuel))

Eq.7 – Moment arm from center of gravity to aerodynamic center of gravity of horizontal tail

l_(HT) =cght-cg2

Eq.8 – Moment arm from center of gravity to aerodynamic center of gravity of vertical tail

l_(VT) =cgvt-cg2

Eq.9 – Planform area of horizontal tail

S_(HT) =(V_(HT) cS)/(l_(HT))

Eq.10 – Sideview area of vertical tail

S_(VT) =(V_(VT) bS)/(l_(VT))

Eq.11 – Neutral point location

x_n =(sm*c)+cg2

Eq.12 – Longitudinal position of wing aerodynamic center

(x_(ac) )_(wing) =x_n -V_(HT)

Resource:

Anderson, John D. “Chapter 8.” Aircraft Performance and Design, McGraw Hill Education, 1999.

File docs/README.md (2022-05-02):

---
home: true
heroImage: /logo.png
heroText: OpenUAS
tagline: Designing and building a fixed-wing open source UAS ✈️
actionText: Get Started →
actionLink: /intro/
features:
- title: Affordable
  details: Low cost, and accessible to all!
- title: Repairable
  details:  Replacement parts easily manufacturable or easily sourced!
- title: Open Source
  details: No proprietary parts or software! All open standards and freely modifiable. 
footer: Iowa State University | Copyright © 2018-present
---

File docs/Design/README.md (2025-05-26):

# Design
<!-- last updated: 4/2/24 -->

## Introduction
The OpenUAS Design team utilizes SolidWorks to model the UAV designs. The team has created 4 versions: OpenUAS 1.0, 2.0, 3.0, and 5.0 (under-development) which can be looked at in more detail on the left side of your screen. The Design team is also implementing computational fluid dynamics (CFD), using StarCCM+, in their considerations with modifying designs prior to and following flight tests. This allows the team to look at pressure data, for example, to modify existing parts before flight.

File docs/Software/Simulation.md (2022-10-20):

# Gazebo Simulation

We are experimenting with using simulation models to test software changes and potentially train pilots. This area still needs further development to be fleshed out more. 

TODO

## Dev Tool Setup for Simulation
This section assumes you already have [setup dev tools for PX4](PX4.md#dev-environment-setup).

Gazebo is a linux only application so we will be running it either through WSL 2 or natively on linux:

::: warning
If you plan to use Docker to run the simulation, there are only docker containers for Gazebo 9 and Gazebo 11. Local and Docker versions of gazebo must match to work correctly. The docker script will attempt to find the verison on you machine, otherwise it will default to Gazebo 9. You can check your local gazebo version by running `gazebo --version`
:::

### Windows with WSL 2
Depending what version of windows you are using, some additional setup may be needed

**Windows 11**
1. Open a terminal into Ubuntu
2. Install Gazebo 9 and Gazebo 9 dev files
    1. `sudo apt update`
    2. `sudo apt install gazebo9`
    3. `sudo apt install libgazebo9-dev`
3. Check that the Gazebo GUI launches by running `gazebo` GUI support for WSL 2 should be included in Windows 11.

**Windows 10**
1. In Windows, download and install VcXsrv, [SourceForge](https://sourceforge.net/projects/vcxsrv/)
2. Run and configure `Xlaunch` application from windows.
    - Select `multiple windows`, next
    - Select `Start no client`, next
    - Uncheck `native opengl` and check `Disable access control`, next
    - Save the configuration file somewhere accessible like your desktop. Run the configuration file to launch VcXsrv quickly in the future.
    - Finish
3. Open a terminal into ubuntu
4. Install Gazebo 9 and Gazebo 9 dev files
    1. `sudo apt update`
    2. `sudo apt install gazebo9`
    3. `sudo apt install libgazebo9-dev`
5. Add the following to the bottom of `~/.bashrc` using your favorite text editor (nano is easy if you have no preference)
    ```bash
    export GAZEBO_IP=127.0.0.1
    export DISPLAY=$(cat /etc/resolv.conf | grep nameserver | awk '{print $2}'):0
    export LIBGL_ALWAYS_INDIRECT=0
    ```
    - This configures the GUI to be forwarded to the VcXsrv and displayed by windows.
6. Run the following to reload .bashrc and make the changes take effect, `source ~/.bashrc`
7. Check that the Gazebo GUI launches by running `gazebo`

::: tip
You must go through the configuration for Xlauch every time you reboot windows.
You can save the configuration file on the last step in Xlaunch and run that instead to speed things up.
:::

### Ubuntu 18.04/20.04 Native/Virtual Machine
1. No additional setup required.

## Building PX4 and Running the Simulation

### Without Docker

**Ubuntu 18.04/20.04 Native/Virtual Machine**
1. Open a terminal to the root of the PX4 firmware
2. Run `make px4_sitl gazebo_open_uas` to build and launch the OpenUAS gazebo simulation

### Using Docker Toolchain
::: warning
There are only docker containers for Gazebo 9 and Gazebo 11. Local and Docker versions of gazebo must match to work correctly. The docker script will attempt to find the verison on you machine, otherwise it will default to Gazebo 9. You can check your local gazebo version by running `gazebo --version`
:::
**Linux**
1. Open a terminal to the root of the PX4 firmware
2. Run `./Tools/docker_run.sh make px4_sitl gazebo_open_uas` to build and launch the OpenUAS gazebo simulation server in docker
    - If you get compilation errors, it can be a good idea to run `./Tools/docker_run.sh make clean px4_sitl` to put the build process in a clean state
3. Open a new terminal and run `export GAZEBO_MASTER_IP=172.17.0.2`
    - This is the public IP address for the container we just made. The public IP address gazebo uses is printed out when the server first starts up in docker
    Gazebo Public Address
    - This value can also be verified by running the following, substituting in the id of your new container
    ::: v-pre 
    `docker inspect --format '{{ .NetworkSettings.IPAddress }}' container_name_or_id` 
    ::: 
4. Run `export GAZEBO_MASTER_URI=$GAZEBO_MASTER_IP:11345`
5. Run `export GAZEBO_MODEL_PATH=~/git/PX4-Autopilot/Tools/sitl_gazebo/models/`
    - Replace first part of path as needed to point to your local PX4-Autopilot directory
6. Run `gzclient --verbose` to launch the gazebo GUI client, and connect to the docker server

**Windows with WSL2**
:::warning
Performance is currently an issue with Gazebo GUI running on WSL 2. Still investigating.

The issue comes from WSL 2 not using hardware acceleration when rendering GUI graphics. This could be better on Windows 11 but have not tested yet.
:::
::: details
**Gazebo working** under docker installed directly in WSL2 from docker [linux installation instructions](https://docs.docker.com/engine/install/ubuntu/). Had to run the docker container under the 'host' network to allow access to all the ports for gazebo to operate. Running under bridge with only port 11345 published did not work.

Current issue with configuration is performance, gazebo client running from WSL with docker gazebo server, sits at about 10 fps circling the iowa aeromodelers field when running maximized on my 21:9 monitor (smaller client resolution helps a lot). The performance drop from running gazebo server in docker compared to running gazebo client and server in wsl is minimal (1 to 2 FPS). However, running the same scenario on linux on bare metal with Nvidia drivers gives 62 fps. Additioanlly, running the docker container for the gazebo server on linux bare metal, does not significantly impact fps, so this is likely an issue with wsl.
:::

The Windows with WSL2 instructions are largely the same as the Linux instructions, except for running VcXsrv and steps 2 and 3.

- Step 0, if you're running on windows 10, make sure your xServer in windows is running by launching XLaunch or running your config file, see [Windows 10 setup](#windows-with-wsl-2)
- In step 2 instead run `DOCKER_OPTIONS="--network host" ./Tools/docker_run.sh make px4_sitl gazebo_open_uas`
- In step 3, the IP address may change between docker instances, check the address each time when gazebo server launches in docker
    - The IP changes due to running on the host network, but is required to get allow gazebo client to access all the ports it needs to, see [Question #166](https://github.com/gazebosim/gz-transport/issues/166) for more details.

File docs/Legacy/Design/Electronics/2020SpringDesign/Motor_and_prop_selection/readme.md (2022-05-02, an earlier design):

# Motor selection process
TODO:
- Using motocalc
- using the motocalc comparison script

Starting with our CFD data, we can use a Thrust equals drag approximation to estimate the thrust requried at a given Velocity. The equation used is:
- insert thrust req equation

Where:
- v is velocity
- rho is density
- W is weight
- e is the oswald efficiency
- Sref is planform wing area
- CD0 is the zero lift drag coefficient. (this can be found as the minimum of the CD vs alpha polar and is the number we need from CFD)

We can also use this curve to find our max endurance and max range cruise velocities. Max endurance happens at the minimum power draw. This can be found by multiplying the thrust required curve by velocity again, and finding the minimum of the curve. Max range occurs at the of the thrust requried curve
Plotting this for a range of velocities and using our aircraft CD0 value generated from CFD, we get this curve:
- insert thrust req curve

Using our Max lift coeficient CLmax, we can find our stall velocitie as well. The stall velocity is higher than both cruise velocities, so an arbitray velocity was picked by the pilot that was a comfortable distance above stall velocity. This is 45 mph.

# Motocalc ouput summary
*note, current is in units 
of amps, and efficiency is in percent effeciency. The current is the current draw from the battery and the efficiency is the total efficiency (i.e) eta_prop\*eta_motor*
## Badass 560kv motor:
### script output
~~~
Current draw at Cruise for Badass 560 12x10: 5.1 
Current draw at Cruise for Badass 560, 13x10: 5 
Current draw at Cruise for Badass 560, 14x10: 4.7 
Current draw at Cruise for Badass 560, 14x12: 4.5

Efficiency at Cruise for Badass 560, 12x10: 53.6 
Efficiency at Cruise for Badass 560, 13x10: 53 
Efficiency at Cruise for Badass 560, 14x10: 51.6 
Efficiency at Cruise for Badass 560, 14x12: 55.5
~~~
### summary
Lowest current draw: 14x12 @ 4.5

Highest Efficiency: 14x12 @55.5

## Badass 650kv motor:
### script output
~~~
Current draw at Cruise for badass 650, 12x10: 5.1 
Current draw at Cruise for badass 650, 13x10: 4.7 
Current draw at Cruise for badass 650, 14x10: 4.4 
Current draw at Cruise for badass 650, 14x12: 4.9

Efficiency at Cruise for badass 650, 12x10: 54.2 
Efficiency at Cruise for badass 650, 13x10: 53.6
Efficiency at Cruise for badass 650, 14x10: 51.5 
Efficiency at Cruise for badass 650, 14x12: 57 
~~~
### summary
Lowest current draw: 14x10 @4.4

Highest Efficiency: 14x12 @57

## Badass 710kv motor:
### script output
~~~
Current draw at Cruise for Badass 710kv, 12x10: 4.8
Current draw at Cruise for Badass 710kv, 13x10: 4.8
Current draw at Cruise for 14x10, 14x10: 4.9
Current draw at Cruise for Badass 710kv, 14x12: 4.5

Efficiency at Cruise for Badass 710kv, 12x10: 56
Efficiency at Cruise for Badass 710kv, 13x10: 55.8
Efficiency at Cruise for 14x10, 14x10: 55.4
Efficiency at Cruise for Badass 710kv, 14x12: 57.3
~~~
### summary
Lowest current draw: 12x10&13x10 @ 4.8  
Highest Efficiency: 14x12 @ 57.3
## Hacker A30-10XL v4 motor:
### script output
~~~
Current draw at Cruise for Hacker 900kv, 12x10: 5.2
Current draw at Cruise for Hacker 900kv, 13x10: 4.8
Current draw at Cruise for Hacker 900kv, 14x10: 5.2
Current draw at Cruise for Hacker 900kv, 14x12: 5.2
Current draw at Cruise for Hacker 900kv, 15x8: 4

Efficiency at Cruise for Hacker 900kv, 12x10: 54.2
Efficiency at Cruise for Hacker 900kv, 13x10: 53.3
Efficiency at Cruise for Hacker 900kv, 14x10: 53.5
Efficiency at Cruise for Hacker 900kv, 14x12: 55.9
Efficiency at Cruise for Hacker 900kv, 15x8: 37.9
~~~
### summary
Lowest current draw 15x8 @ 4

Highest Efficiency 14x12 @ 55.9
## Badass 790kv motor:

### script output
~~~
Current draw at Cruise for badass 790, 12x10: 5.1 
Current draw at Cruise for badass 790, 13x10: 5.2 
Current draw at Cruise for badass 790, 14x12: 5.8
Current draw at Cruise for badass 790, 15x8: 4.5 

Efficiency at Cruise for badass 790, 12x10: 51.2 
Efficiency at Cruise for badass 790, 13x10: 51.1 
Efficiency at Cruise for badass 790, 14x12: 55.1 
Efficiency at Cruise for badass 790, 15x8: 34.3
~~~

### summary
Lowest current draw: 15x8 @4.5

Highest Efficiency: 14x12 @55.1
## Badass 970kv motor:

### script output
~~~
Current draw at Cruise for badass 970, 12x10: 5.4
Current draw at Cruise for badass 970, 13x10: 5.5
Current draw at Cruise for badass 970, 14x10: 5.3
Current draw at Cruise for badass 970, 14x12: 5.5
Current draw at Cruise for badass 970, 15x8: 5.2

Efficiency at Cruise for badass 970, 12x10: 48.4
Efficiency at Cruise for badass 970, 13x10: 48.5
Efficiency at Cruise for badass 970, 14x10: 47.4
Efficiency at Cruise for badass 970, 14x12: 50.8
Efficiency at Cruise for badass 970, 15x8: 34.2
~~~
### summary
Lowest current draw: 15x8: 5.2

Highest Efficiency: 14x12 @ 50.8

### Analysis of prop/motor combinations
TODO:
- talk about most efficient prop and motor
- talk about how 970 and 15x8 have the most excess thrust
- talk about why we chose the least efficient motor

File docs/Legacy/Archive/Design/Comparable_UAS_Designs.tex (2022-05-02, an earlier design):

\documentclass{article}
\usepackage[margin=1in]{geometry}

\begin{document}

\title{\textbf{Comparable UAS Designs}}
\author{OpenUAS Team}
\maketitle

This document lists the specifications of other current Small Unmanned Aircraft Systems (SUAS).

\section{RQ-14A Dragon Eye}

This UAV was created by the Naval Research Laboratory and the Marine Corps Warfighting Laboratory. The Dragon Eye is used by the United States Marine Corps.\\\\
\textbf{Wingspan:} 3.75 ft\\
\textbf{Weight:} 5.9 lb\\
\textbf{Payload:} \\
\textbf{Length:} 3.0 ft\\
\textbf{Height:} 11 in\\
\textbf{Launch Method:} Hand or bungee\\
\textbf{Materials:} Carbon fiber, plastic, aluminum, copper, rubber, styrofoam\\
\textbf{Power Plant:} Two battery powered motors\\
\textbf{Fly Time:} Approx. 1 hr\\

\textbf{Source:} Smithsonian National Air and Space Museum

\section{Razor}

This UAV was created by the University of Virginia for the Department of Defense. The Razor has a flying wing design.\\\\
\textbf{Wingspan:} 4 ft\\
\textbf{Weight:} 6 lb\\
\textbf{Payload:} Up to 1.5 lb\\
\textbf{Length:} \\
\textbf{Height:}\\
\textbf{Launch Method:} Hand or bungee\\
\textbf{Materials:} 3-D printed plastic\\
\textbf{Power Plant:} \\
\textbf{Fly Time:} Approx. 45 min\\

\textbf{Sources:} University of Virginia Link Lab, Additive Manufacturing

\section{FQM-151A Pointer}

This UAV was created by AeroVironment Inc. and is used by the Army and the Marine Corps. This is an older system, first used by the military in 1990. It is still in use today, however, this UAV is being replaced by other models.\\\\
\textbf{Wingspan:} 9 ft\\
\textbf{Weight:} 9.6 lb\\
\textbf{Payload:} \\
\textbf{Length:} 6 ft \\
\textbf{Height:}\\
\textbf{Launch Method:} Hand\\
\textbf{Materials:} \\
\textbf{Power Plant:} One battery (lithium) powered motor\\
\textbf{Fly Time:} Approx. 1 hr\\

\textbf{Sources:} Designation Systems, Wikipedia

\section{RQ-11B Raven}

This UAV was created by AeroVironment Inc. and is used by the United States Military.\\\\
\textbf{Wingspan:} 4.5 ft\\
\textbf{Weight:} 4.2 lb\\
\textbf{Payload:} 6.5 oz\\
\textbf{Length:} 3 ft \\
\textbf{Height:}\\
\textbf{Launch Method:} Hand\\
\textbf{Materials:} \\
\textbf{Power Plant:} One electric motor using rechargable lithium ion batteries\\
\textbf{Fly Time:} Approx. 1 to 1.5 hr\\

\textbf{Source:} AeroVironment

\section{Parrot Disco FPV}
This is a commercial UAV created by Parrot.\\\\
\textbf{Wingspan:} 3.75 ft\\
\textbf{Weight:} 1.65 lb\\
\textbf{Payload:} \\
\textbf{Length:}  \\
\textbf{Height:}\\
\textbf{Launch Method:} Hand\\
\textbf{Materials:} Plastic foam \\
\textbf{Power Plant:} \\
\textbf{Fly Time:} Approx. 45 mins\\

\textbf{Sources:} Parrot, CNET

\end{document}

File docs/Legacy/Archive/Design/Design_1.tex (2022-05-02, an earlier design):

\documentclass{report}
\usepackage[utf8]{inputenc}

\title{Design 1}
\author{Catherine Sener}
\date{January 2019}

\begin{document}

\maketitle
\tableofcontents

\chapter{Introduction}
\section{Requirements}
\begin{itemize}
    \item Configurable: Wings can be changed
    \subitem The fuselage was designed such that the wing slots are square. The point of the square wing slots was to make it easy to change the wing design. With each new design the fuselage could be reused, and a new wing mount would have to be made. The wing mounts would be able to fit easily in the square slots and Velcro would be utilized to hold the wings in place as well as the inside shape of the fuselage cut. 
    \item Can break down and moved easily
    \subitem In order to make the UAS easily movable, it can be broken down. The tail can come off by removing the carbon fiber rod from the fuselage. The fuselage can be split in half, which also allows ease of changing electronics. The wings can also come off.
    \item Simple assembly
    Just like it is easy to be broken down the UAS is also easily assembled. The wing mounts pop in place are held by strapping the two halves of the fuselage together. The tail easily slides into the fuselage and is held in place by straps.
    \item Does not require a runway
    \subitem Runways are pricey to reserve and are not always available where you want to launch, so it is easier if the UAS does not require a runway and can be hand launched. This is why the UAS has a weight limit of 25 lb, absolute maximum. With current electronics and shell it weighs about 10 lbs. If at its absolute maximum weight of 25 lb, it will require a launch system in order to take off. This will be a slingshot like structure. A bungee cord attached to a ramp at an angle would be armed and be able to launch the UAS at it's required speed in order to generate lift. 
    \item Can be manufactured by hobbyist
    \subitem Options were explored to let the UAS be created by hobbyist. This is hwy it was made out of accessible materials such as foam, balsa, monokote, and 3D printed materials. While it is not he cheapest to manufacture, it is possible to do at home with tools that are accessible to the general public.
    \item Can withstand a crash landing
    \subitem The UAS does not have any landing gear to conserve weight since it also does not require a runway to take off. This means that while landing, the UAS will have to be "crashed landed" in a field or a bush or a net. Therefore, the UAS must be able to withstand multiple crash landings and be easily repairable. 
\end{itemize}
\chapter{Design}
\section{Structure}
The requirements of the UAS had some structural challenges. The structure had to be aerodynamically efficient for something that weighed under 5 lbs and could carry an electrical payload of about 10 lbs. The fuselage space had to be able to hold at least 2 batteries approximately 2 X 6 X 1.5 in each, a motor, a raspberry pi, and a few other configurable electronic options while being able to house wires efficiently and still have enough room to proved cooling air to the batteries. The inside of the fuselage had to be easily accessible, the wings and the motor could be replaced, and we plan on crash landing the UAS which meant its underbelly had to be thick enough to withstand in pact.
\\
\subsection{Fuselage}
To meet requirements, the fuselage was made to be a large cylinder with a flat thick belly. its outside diameter is approximately 7in large, and has a length of about 12in. For a long time it was debated weather or not to put ski like skids on the bottom of the fuselage for extra height on landing to protect the propeller from the ground and provide an extra crush zone. This idea was turned down due to the extra drag it would produce.
\\
\\For easy access the fuselage is cut in half. Hinges will be added to one side while latches will be added to the other so the fuselage can be opened like a box when electrical equipment needs to be changed.
\\
\\The generic rectangle cut out on the fuselage is meant for the configurable wings. The idea is that every time we want to change the wings these rectangular blocks can be cut out of foam and manually shaped to the shape of our airfoil.
\\
\\The motor mount on the front is currently designed for just one motor in particular with an inch diameter. Theoretically what would be done for different motors would be to make the hole larger, and then come up with a separate mounting block for smaller motors while larger ones would fit perfectly into the nose of the UAS.
\subsection{Wings}
\subsection{Tail}
\section{Material}
As far as materials go I believe our initial selection was a mistake. We planned on using EPS and XPS foam for most of our structure. While this material is very light it is also not too strong. Another error we made was trying to hotwire EPS foam as well. The hotwire severed and then melted the low budget foam back together practically making it useless. 
\\
\\For the wing section we were originally going to use foam as well. However, since the hotwire failed to cut the proper airfoil shape we decided to do a rib design instead. The balsa wood pieces were cut from 1/8th in thickness. These pieces were cut from a CNC machine which caused some of the pieces to split and all pieces needed to be sanded down and smoothed. Looking back it would have probably been better to lazer cut the pieces of balsa in order to get a clean and precise cut. 
\\
\\Once the airfoil cut outs were complete for the wings, the pieces were glued to a wooden rod at the leading edge, and a carbon fiber rod at the trailing edge. In order to get the flaps to work, they were glued to the carbon fiber rod while the full airfoil cut outs were not glued to the carbon fiber rod. This made it so the rod would rotate freely threw the airfoil but pivot the flaps.
\\
\\Monokote was used to cover the airfoil ribs and retain the correct shape. Again, in order to allow the flaps to move correctly they were monokoted separately from the wings to allow freedom of movement.
\\
\\A similar strategy to the wing section was originally applied to the tail section. However, the pieces were so small they could not be cut out of balsa wood. Thanks to the Aerostruder nozzle for our 3D printer, we were able to print out the horizontal and vertical tail sections with little to no trouble. Some pieces still required to be filed down in order to fit on the carbon fiber rods properly.

\section{Manufacturing}
\begin{itemize}
    \item 3D printing components
    \item CNC the balsa wood airfoils
    \item Outsourced foam cutting to ISU lab
\end{itemize}
\chapter{Pros/cons}
\textbf{Pros}
\begin{itemize}
    \item Configurable, wings can be changed.
    \item Electronics are accessible
    \item Design can be taken apart and transported easily
\end{itemize}
\textbf{Cons}
\begin{itemize}
    \item Connecting joints are not structurally stable.
    \item fuselage is bulky and causes unnecessary turbulence.
\end{itemize}

\end{document}

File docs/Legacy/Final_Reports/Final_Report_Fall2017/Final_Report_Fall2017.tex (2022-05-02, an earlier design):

\documentclass{article}
\usepackage[utf8]{inputenc}
\usepackage{lstautogobble}
\usepackage[export]{adjustbox}
\usepackage{graphicx}
\usepackage{changepage}
\usepackage{listings}
\usepackage{amsthm}
\usepackage{subcaption}
\usepackage{amssymb}
\usepackage{titlesec}
\usepackage{hyperref}

%Command to change name of table of contents
\renewcommand*\contentsname{Table of Contents}

%Command to start sections on new pages
\newcommand{\sectionbreak}{\clearpage}

%Create a new "Unlabeled section" that will be added to toc but not printed
\newcommand{\unlabeledsection}[1]{%
 \clearpage
  \par\refstepcounter{section}% Increase section counter
  \sectionmark{#1}% Add section mark (header)
  \addcontentsline{toc}{section}{\protect\numberline{\thesection}#1}% Add section to ToC
  }
  
\emergencystretch=1em

\title{OpenUAS:\\First Semester Progress Report }
\begin{document}

%%TITLE PAGE%%
\maketitle

\newpage

%%TEAM PAGE%%
\begin{center}
\Large \textbf{The OpenUAS Team}

\vspace{1cm}

\large{
Abigail Gries\footnote[1]{ISU Department of Aerospace Engineering}\\ Logan Gross\footnotemark[1]\\ Alex Harpenau\footnotemark[1]\\ Madison Harrington\footnotemark[1]\\ Mandy Kewitsch\footnotemark[1]\\ Catherine Sener\footnotemark[1]\\ Josh Wallin\footnote[2]{ISU Department of Electrical and Computer Engineering}
}\par

\end{center}

\newpage

%%TABLE OF CONTENTS%%

\tableofcontents

%%PROJECT OVERVIEW%%
\section{Project Overview}

\subsection{Purpose}
Currently, there are no open-source unmanned aerial systems (UAS) which are fixed-wing and conceptually accessible available to the general public. There are some similar UAS which are available, but they must be purchased and are not open-source. OpenUAS is producing an open-source, commercial off-the-shelf (COTS) UAS that can be used for recreational and research purposes, and it will only consist of components available to the general public, including open-source software.

\subsection{Scope}
In order to develop an open-source, COTS UAS for recreational and research purposes that is free and available to the general public, a list of objectives, deliverables, and constraints were identified at the conception of the project. The following section will provide an overview of these lists.

\subsection{Objectives}
\begin{enumerate}
\item Create an open-source, COTS UAS for short recreational and research flights
\item Provide full documentation of the conception, design, and testing of all systems
\item The UAS should not require a runway for takeoff or landing
\item The piloting of the UAS shall be accessible to hobbyists
\item The UAS shall be made of ``affordable" components
\item UAS components should be reconfigurable and support additional components
\end{enumerate}

\subsection{Deliverables}
\begin{enumerate}
\item A functioning design and prototype of a UAS
\item A ground launch system for takeoff
\item Relevant tools for piloting the UAS from the ground
\item Extensive documentation of the development process
\item Extensive documentation on proper use and safety
\end{enumerate}

\subsection{Constraints}
\begin{enumerate}
\item COTS components
\item Affordable components
\item Easily duplicated components (e.g. all 3D printed parts can be reasonably produced by hobbyists)
\item All components should be reasonably safe (e.g. battery)
\item Design and testing completed within 1 academic year
\end{enumerate}

%%BACKGROUND%%
\section{Background}

\subsection{Related Work}

%%PROJECT DOCUMENTATION%%
\section{Project Documentation}

Varying forms of documentation were developed in order to assist with tracking the vision, objectives, high-level project plan, meeting documents to capture insight and actions needed, and so forth. The documentation is intended to not only support the systems engineering aspect of the project, but also serve an educational purpose by assisting future users who would like insight into what efforts and decisions were made to bring OpenUAS from a concept to a reality.

\begin{enumerate}
\item \textbf{Tollgate} \\Tollgates show what team member has primary responsibility for completing certain tasks, how team members / subsystems are cross-functional and share responsibility with completion of tasks, and also track what deliverables are associated with each objective. The Tollgates were set up to indicate the completion of major milestones, or ?phases?. Project Kick-Off has been completed, and Conceptual Design Review is currently being focused on as the semester reaches a close. Later, the Preliminary Design Review and Systems Design Review phases will be completed.
Tollgates become very helpful as a design begins to develop and ?take shape?, as it becomes a high-level review of what work has been accomplished. Each Tollgate has a list of ?Deliverables?--objectives that would show the project is ready to move to the next phase once all are completed. In order to show the deliverable is completed, ?objective evidence? is provided. (Example: ?Initiate Requirements? is a deliverable, and a requirements document would be the objective evidence.) The team must be in consensus that each deliverable has been met appropriately and that the project is on track to meet its objectives and purpose.
\item \textbf{Running Action Item List} \\The Running Action Item List (RAIL) is to be updated regularly with tasks as they come up. This is attached to the overall Tollgate document. Action items can be assigned to individuals or to the team, with an expected completion date.
The RAIL is not to be considered the same as ?Deliverables? and ?Objective Evidence? from the Tollgate document, although it should be noted that the objective evidence is often worked on as an action item. Many times, action items are assigned after team meetings to help ensure progress continues to be made.
\item \textbf{Project Charter}\\ This is a ?one-pager? intended to help provide a broad overview of the project. The Project Charter lays out the team, the scope of the project, the purpose, and so forth. Additionally, the project objectives, deliverables, and constraints that were mentioned earlier in this paper come from the Project Charter as it maintains the vision and intent of the OpenUAS project.
\item \textbf{Requirements}\\ The requirements document is currently a ?living? document that is still in progress. It includes the overall system requirements, as well as subsystem requirements. The requirements document helps guide the team in design decisions, but also has undergone multiple reviews, including one major peer review, to ensure that they are reasonable, feasible, and assist in meeting the overall project objectives. They are being updated to reflect the ?Easy Approach to Requirements Syntax? (EARS) format, which involves providing precise language and rationale. The revisions are maintained on GitHub.
\item \textbf{Weekly Meeting Agenda \& Minutes}\\Each week, Meeting Minutes are held to capture what discussion and decisions occurred. The tasks of leading the meeting and taking meeting minutes are rotated through the team. The one leading the meeting will set the agenda for that meeting?s primary discussion points, and the meeting minutes are taken in ?real-time? on the shared Google Drive. Afterward, the meeting minutes are then cleaned up and formatted into the meeting minute document kept on GitHub.
\item \textbf{Project Plan}\\ The Project Plan is a long-term, high-level calendar broken down by month and then broken down weekly with goals and deliverables. This document is maintained on GitHub. Every few weeks the team will make a plan for the next few months.
\item \textbf{Requirements}\\ The requirements document is an extensive, volatile artifact that has been developed since the beginning of the project. Originally, our primary requirements were high-level, and directly traceable to the overall project goals. Now, as we begin to make decisions about what our design will look like, the requirements have evolved to become more detailed. For the sake of making requirements easier to read and understand, we chose to use the EARS \cite{Terzakis2013} requirements syntax.
\end{enumerate}

\section{Related Work}
\noindent Currently, there are very few comparable fixed-wing UAS. The United States uses UAS such as the RQ-14A Dragon Eye and RQ-11B Raven in its military. Although these UAS are similar in size and weight to the OpenUAS team's target design, the technology and capabilities of these systems are much more advanced, and as such, the budget well exceeds the team?s overall budget.\\

\noindent The University of Virginia created the Razor, a small fixed-wing UAS for the Department of Defense. This UAS has a flying wing design and utilizes an Android phone as the main processor. The Razor is of similar size, weight, and performance of the team?s target design. One main difference in this system is that it is entirely 3D printed. The team plans on utilizing 3D printing, but not to the extent of the Razor design.\\

\noindent The Albatross is a commercial UAS produced by Applied Aeronautics. Although this aircraft is slightly larger than the team's target design, its performance and low-cost are comparable to the team's goals. This UAS is described in more detail later in the paper, as the team purchased and is beginning to study this design. \\

%%LAB SETUP AND ORGANIZATION%%
\section{Lab Set-Up \& Organization}
\noindent The lab provided this semester began with no equipment. Throughout the semester, orders had been placed for tools and other items needed in order to ensure a work space that has all tools needed for successful progression of this project. Because we are working within a large organization, special documentation and communication must be done in order to acquire the parts needed for the lab. This includes confirmation of successful retrieval of parts and checking if damage was done to them. If damage is found, proceeding with the proper return process and notifications so everyone knows how parts are moving about. \\

\noindent In order to organize and track many of the lab?s tools, inspiration was taken from toolbox kits. In order to maintain a visual inventory of smaller tools that could go missing or be misplaced, foam was ordered and will be sized into drawers through the lab. Each drawer will be categorized in a way that makes sense, and tools or items that fit within that category will have their shape cut into the foam. This allows an individual to open a drawer and see at any moment what tools or items are available (or may be missing), it also ensures the tools or items are kept in a spot where they are protected from damage (or kept from damaging other items).\\

\noindent In order to work with simulations, run flight software, and test certain electronic components, the team needed computers. Dr. Rozier,  the Principal Investigator of the project, ordered and set up four computers using Linux operating systems.These computer would then be used by all teams using the lab. Since then, the team has converted one computer to be used mostly for the UAS project, 3D printing, and battery charging, while using another for communication with members remotely. Another computer is restricted due to projects being done on it, and the fourth is open for all team. The 3D printing computer will be moved once proper cables are put in place for internet connection, and will remain separated from the other three in order to better streamline movement within the lab. It will also sit directly across from the sink in order to move 3D printed parts over for cleaning and processing. \\

\noindent One large purchase made for the lab was the purchase of the 3D printer. The team considered several different options before purchasing the LulzBot Taz 6 3D printer. The decision to purchase this specific printer was made for several different reasons. The primary reasons were: it has one of the largest print volumes for its cost, it was recommended by faculty at Embry-Riddle Aeronautical University, one of the team members had already worked with this model, and there were many positives reviews for it on the internet. Unfortunately, the printer came to the team damaged and had to be returned. A new printer was then sent to the lab again, and was able to be assembled and used correctly.\\

%%INSPIRATION: THE ALBATROSS%%
\section{Primary Inspiration: The Albatross UAV}
\noindent The team decided to purchase the Albatross, a low-cost, entry-level drone produced by Applied Aeronautics \cite{AlbatrossFAQ}, in order to have a model for testing ideas for the OpenUAS. Specifically, the team wanted to observe the flight characteristics such as power, controllability, maneuverability, speed, and airfoil characteristics. The team also wanted to order this model to look at the material of the structure, the inside configuration, the weight, and how easy it was to assemble. After purchasing, the Albatross parts were delayed in shipping. The team received all parts before the end of the semester, but is planning to contact Applied Aeronautics for instructions before beginning to assemble the Albatross.\\

\noindent Thus far, the team has liked the interior mesh for supporting the electronics inside. Looking forward, the team is going to assembly and perform multiple flight tests to answer the specific subsystem questions the team had for designing the OpenUAS. 

%%SYSTEM ARCHITECTURE AND PROGRESS%%
\section{OpenUAS System Architecture \& Progress}
\noindent The OpenUAS team divided the entire system into six subsystems: Structures, Software, Controls, Electronics, Propulsion, and Ground System. The entire system completed 3 requirement revisions with added rationale.The OpenUAS will be modeled by the Albatross, created with support from the Lulzbot 3-D Printer, and utilize the best, most accessible most accessible characteristics of fixed-wing UAS. More details on the OpenUAS system is discussed below in the corresponding subsystems. \\

\begin{figure}
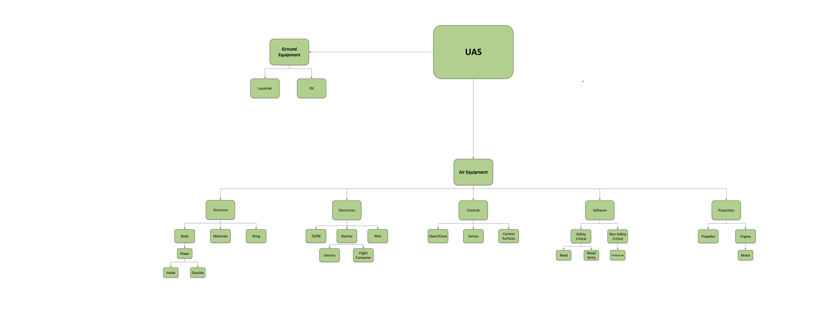
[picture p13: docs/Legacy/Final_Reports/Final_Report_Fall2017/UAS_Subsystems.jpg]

\caption{Initial version of system architecture}
\centering
\end{figure}

\subsection{Structures}
\noindent The first step in the development of the structures subsystem was the creation of the structures? requirements. The requirement process is discussed in greater detail in the requirements section of this document. For the structures? requirements specifically, there are currently 25 requirements that have gone under numerous revisions and one formal peer review. There is also rationale written for each requirement, and the requirements are parametrized as needed. \\

\noindent After the preliminary round of structures? requirements was drafted, the next big step was determining a preliminary estimate of the total weight of the UAS. This step was key in the progress of the project because an estimate of the weight was needed to make successive design decisions from both a structural perspective and electronics perspective. This estimate of weight was determined using several different approaches. First, an estimation of the weight of the electronics and battery was determined from specifications of commonly used components on UAVs. Then, several combinations of wingspan, wing planform area, and the resulting aspect ratio were identified. Additionally, the maximum W/S ratio of the Albatross UAV was calculated. Using these combinations coupled with a W/S ratio slightly less than the Albatross, a maximum weight estimation was determined for each combination of wingspan, wing area, and aspect ratio.\\

\noindent The maximum weight calculated for each scenario was then compared to the sum of the estimated structural, electronic, and battery weights. The most favorable combination was selected. This configuration of the UAS requires a 5 ft wingspan and 2 ft wing platform area, creating an aspect ratio of 12.5, and allowing a maximum takeoff weight of 6 lbs. The estimations for weights were as follows: battery weight of 1.5 lbs, electronics weight of 1.5 lbs, and structural weight of 2.05 lbs, for a total weight of 5.05 lbs. This allows for almost 1 lb of ?wiggle? room in the weight for estimation error or additional components. \\

\noindent The team decided that for the first design of the UAS, the wings would be constructed of foam. This decision was made based on the ease of working with foam, how light it is, and the availability of foam to an average hobbyist. The two choices of foam were expanded polystyrene (EPS) and expanded polypropylene (EPP). EPP was chosen as the foam for the wing as it is very durable and easily repaired. However, this foam is also very flexible. Due to this, research was also done into ways to reinforce EPP foam wings. Currently, the team is considering using carbon fiber wing spars to reinforce the wings. \\

\subsection{Software}
\noindent Our goals for software this semester were twofold: to develop useful requirements, outlining the proposed behavior of our flight software, and to select an existing, open source option for use onboard our aircraft. To satisfy this first goal, we continuously developed a requirements document (found on the team Git repository), applying the EARS requirements capture technique. Our hope is that, with more time, we may take advantage of the suite of tools specifically used for realizability checks on formally structured requirements.\\

\noindent Upon completing our research of open source flight software options, we chose PX4 (https://github.com/px4/Firmware/), a community-developed autopilot for UAS. PX4 contains not only the necessary components for manual, but also autonomous flight. As we had debated the level of autonomy for our final product, this degree of freedom will be useful. The open source nature of PX4 allows for it to be continuously developed by hobbyists and professionals in the field; the well-structured community ensures that PX4 becomes more and more powerful, with approval from a dedicated team required to make substantial changes. Additionally, the flight software can be edited and built in the lab, which should allow us to alter values and behaviors as needed to satisfy our overarching goals. While ArduPilot presented an alternative autopilot software, frequently used in the UAS domain, we felt that PX4 was more well supported, documented, and developed for our chosen flight computer, the Pixhawk. \\

\noindent The Pixhawk is an onboard flight computer that includes a barometer, three degree of freedom (DOF) gyroscope, three DOF accelerometer, and three DOF magnetometer built in, with some redundancy amongst components. Though these sensors are the only ones necessary to fly, we felt that an airspeed sensor would be an asset for our implementation; for hardware-in-the-loop testing through QGroundControl, this sensor was also a necessity. As such, we purchased and integrated one with the flight computer. We felt that the combination of an open source software suite and flight computer allows for maximum customization in this project, especially as we seek to allow for flexibility in the final product (ex. using alternate sensors to satisfy the same goals for PX4).\\

\noindent To test the software on the ground, we are using QGroundControl, run on Ubuntu 17.10 in the lab. The PX4 documentation specifically suggested this application, along with FlightGear, for hardware in the loop testing, since it is free compared to other options. Unfortunately, we struggled to find a way to calibrate the Pixhawk?s sensors and perform testing in QGroundControl, without having to first have the airspeed sensor and radio controller; as a result, we have had to wait until now to begin this full setup process (since both tools have arrived). It is our hope to soon have all components calibrated, off the aircraft, to do some simple simulation of flight and testing of the electronics equipment.\\

\subsection{Controls}
\noindent The team has dedicated 3 requirement revisions for the controls system. While developing these requirements, the team has been researching other fixed wing UAS to develop an understanding of what works best fundamentally for controls.\\

\noindent The development of the controls system requirements concentrated on safety, functionality, and responsiveness. These requirements include further subsystems and rationale for supporting the requirements. Further information of the controls requirements can be found in the requirements section of this report. \\

\noindent The team has decided that for the first prototype, our UAS will utilize ailerons, flaps, and rear controls. This decision was made to provide additional control over the aircraft with minimum additional complexity. The ailerons will be the primary control of the aircraft. Another consideration was made regarding the tail section; to provide aircraft stability, coordinated yaw, and better resistance to cross wind, the team will design our model with an upward ?V? shape for the rear control functions. This design has been historically one of the best models for autonomous flight, and therefore will be incorporated into our first design. The team is considering using this design based on its implementation on the Albatross design. \\

\noindent Some considerations the team has regarding future designs of the UAS include double stacked wings and vertical takeoff and landing. These are both much greater in complexity than desired for the team?s first design, but are still considered for future prospects. The controls system would change substantially for either case, but is something the team looks forward to developing. \\

\noindent The team is still in the process of researching other projects to determine what controls system designs will be utilized. The Albatross is of particular interest to the team and will likely influence control system and structural decisions next semester. The software aspect of the controls is further explained under the software section of this report. \\

\subsection{Electronics}
\noindent After narrowing the overall weight of the UAS to approximately six pounds during the early iterations of the calculated design, the team decided to invest in an Iron Bird model of the UAS for testing. Using the overall weight plus an approximate weight-to-thrust ratio required for minimum takeoff, two motors were selected to fulfill different mission parameters, which are longest flight time and highest attainable velocity. These motors exceeded the minimum required thrust-to-weight ratio so that the UAS may take off in a shorter distance, but also have distinctly different flight parameters for testing the structure and the versatility of the UAS and its customization. Based off of the two motor selections, ESCs, power modules, propellers, batteries and a case to transport the Iron Bird was selected and ordered. Multiple types of propellers were purchased in order in give an even larger envelope for testing the flexibility of the UAS under different conditions. A good example of this is how the propeller characteristics and battery influence flight time, takeoff distance, and max speed. \\

\noindent Due to deciding that the PX4 would be the team?s flight computer, and that the team would be using the Airspeed sensor and other needed parts from the purchased Albatross, the team did not order additional electronics until the team knew what additional parts were going to be tested. All parts currently needed for the Iron Bird version 1 that was ordered separate from the Albatross has been soldered and properly attached to form the first basic testbed system. \\

\noindent As the project develops, more electronics requirements and rationale are added to demonstrate the growth of the understanding and needs of the electronics in the UAS. \\

\subsection{Propulsion}
\noindent The propulsion system considered to be the propellers and the motor. The battery was considered for this system, but placed specifically in the electronics category because it runs more than just the motor. Propulsion is directly influenced by the electronics, and equally influences the electronics system. This is because for this UAS, the propulsion system was decided to be electronic. This decision was made due to the lightness of the motor system, the fixed and lighter weight of the fuel, and attempting to use up-to-date technology. \\

\noindent When choosing what motors were going to be used, a thrust-to-weight ratio and an overall weight approximation of the UAS was used from the structures side of the team. Although originally planned to be a next semester purchase, a request for the Iron Bird version 1 was requested, so a decisions for electronics and propulsion were pushed forward. The propulsion was prioritized over the electronic decision making because a weight and a thrust-to-weight decision had been made, so finding a motor to fit the needs and basing the battery and other needed parts off of the motor made the most sense. Two motors were decided on, one that had a low draw on the battery, but also had the lowest thrust, and another that had higher draw, weighed more, but also had a significantly higher thrust. This allowed us to have a large range of test parameters and flexibility, with the hope that the team could make the UAS fairly customizable while also keeping it affordable. Both motors were fairly inexpensive, and low weight, with the lighter one sitting at twenty grams, and the other just over eighty grams. \\

\noindent Each motor had to separate sets of propeller purchased for them. They both had a higher thrust set and a lower thrust set, with the idea that the motors could be used for multiple roles. In particular, an idea was made to build a contraption that contained the propeller and motor of the smaller set for live testing within the lab of the Iron Bird. This way, the team could test how the controls responded with the controller and any autonomous programs while under standard, constant power draw. \\

\noindent As more iterations of both the requirements of the structures and the calculated characteristics of the UAS change, the requirements of the propulsion have the potential to change due to values falling outside of the expect initial range. Because of that, many of the valued requirements still have variables in place of the number in order for the team to lock in the desired, but also reasonable, requirements for the UAS. \\

\subsection{Ground System}
\noindent The ground system of this aircraft will include features of takeoff, landing, transmitting and receiving, and an assembly kit. The team is still considering different takeoff options such as a catapult launch or runway launch. These different considerations require their own different requirements such as landing gear or some sort of connection to the catapult. Different landing considerations include bush landing, autonomous landing, or parachute landing. The team has decided that our kit for setup shall be complete and support an easy assembly and pre-flight check for the UAS. The team will use the following semester to solidify decisions within the ground system as the preliminary design for the UAS develops. \\

%%LESSONS LEARNED%%
\section{Lessons Learned}
\begin{enumerate}
\item Despite best efforts to set timeline at the beginning of the project, we must be prepared to adapt to unexpected changes.
\begin{enumerate}
\item Getting started can be slow as we work to iron out the details
\item Things can arrive broken and must be sent back
\item Things sometimes don?t arrive at all
\item Outside parties may not always be capable of acting on our timeline
\end{enumerate}
\item Documentation takes a lot of effort \& time, and if not maintained in a ``timely" fashion, can become cumbersome to all.
\begin{enumerate}
\item It?s important to act with due diligence to ensure things are up to date, otherwise we fall behind with tracking our progress and can fail to capture the rationale behind our decisions.
\end{enumerate}
\item Purchase orders are not simple within an organization, and many levels of documentation and rationale must be used in order to obtain needed materials.
\begin{enumerate}
\item Rationale requires comparisons to other products of similar quality and attributes.
\item Extensive research may be needed to find the right products
\item A ``completed" list of items will always need to be amended
\item Multiple item requests are to be expected.
\end{enumerate}
\item Documentation of safety takes much time, especially when online sources have varied (and untested) solutions.
\begin{enumerate}
\item Double check information found in an area that may not be well research
\item Check sources for validity
\item Observe and note inconsistencies in information
\end{enumerate}
\item Soldering takes time and patience.
\begin{enumerate}
\item Having extra hands, mechanical or not, makes the process easier
\item Prepare dummy tests at first so that material isn?t going to waste
\item Always have spares
\end{enumerate}
\item Don?t expect items to come in on-time or intact. 
\item Daily, respectful reminder emails are appreciated.
\begin{enumerate}
\item Professors, Teacher Assistants, Employees, Mentors, and other individuals helping with projects of this scale have other things to work on. Reminders help keep you in the scope of their day to day work.
\end{enumerate}
\end{enumerate}

%%LIST OF FUTURE TASKS%%
\section{Future Tasks \& Deliverables}
\begin{enumerate}
\item Performance analysis of Lithium Polymer batteries versus each other.
\item Performance analysis of Lithium Polymer batteries versus Albatross Lithium Ion trapezoidal battery pack
\item Analysis and study of unexpected weight and performance of two of the Lithium Polymer batteries
\item Design a new airfoil/wing specifically for our UAS
\item 3D print a fuselage
\item Create a launch system
\item Construction of the electronic subsystem within the UAS
\item Complete integration of electronic parts with the control surfaces
\item Further outfit the lab with equipment and computers with needed programs
\item Lab setup completed
\item Final Expanded Battery Safety Documentation
\item Document showing all purchased items for the lab 
\item Document showing successful retrieval of all items 
\item Fully outfitted Iron Bird 
\item Purchase List converted to LaTeX
\item Hardware in the loop testing through QGroundControl and FlightGear. 
\item Flight testing the Albatross
\item Rough Design of UAS
\item Final Design of UAS
\item Flight of UAS
\item Final Documentation of Requirements
\item Final Project Document and Review
\item End of Semester II Paper for Dr. Rozier
\end{enumerate}

%%REFERENCES%%
\unlabeledsection{References}
\begin{thebibliography}{100}
\bibitem{AlbatrossFAQ} Albatross UAV - FAQ. (n.d.). Retrieved December 13, 2017, from \\\url{https://www.appliedaeronautics.com/far/}
\bibitem{Crawley2004} Crawley, E., De Weck, O., Eppinger, S., Magee, C., Moses, J., Seering, W.,Whitney, D. (2004). The Influence of Architecture in Engineering Systems. MIT Engineering Systems Division, 1-29. Retrieved December 11, 2017, from \\\url{http://strategic.mit.edu/docs/architecture-b.pdf}
\bibitem{Terzakis2013} Terzakis, J. (2013). EARS: The Easy Approach to Requirements Syntax. In International Academy, Research, and Industry Association: The Eighth International Multi-Conference on Computing in the Global Information Technology. Retrieved October 11, 2017, from \\\url{https://www.iaria.org/conferences2013/filesICCGI13/ICCGI_2013_Tutorial_Terzakis.pdf}
\bibitem{PX4Git} PX4 Open Source Dev Team. ``PX4." PX4 Pro Autopilot Software, 1.6.5, Github, 11 Dec. 2017, \\\url{github.com/px4/Firmware/}.
\end{thebibliography}

\end{document}

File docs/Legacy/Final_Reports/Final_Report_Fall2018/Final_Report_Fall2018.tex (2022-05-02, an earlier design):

\documentclass{article}
\usepackage[utf8]{inputenc}
\usepackage{lstautogobble}
\usepackage[export]{adjustbox}
\usepackage{graphicx}
\usepackage{changepage}
\usepackage{listings}
\usepackage{amsthm}
\usepackage{subcaption}
\usepackage{amssymb}
\usepackage{titlesec}
\usepackage{hyperref}

%Command to change name of table of contents
\renewcommand*\contentsname{Table of Contents}

%Command to start sections on new pages
\newcommand{\sectionbreak}{\clearpage}

%Create a new "Unlabeled section" that will be added to toc but not printed
\newcommand{\unlabeledsection}[1]{%
 \clearpage
  \par\refstepcounter{section}% Increase section counter
  \sectionmark{#1}% Add section mark (header)
  \addcontentsline{toc}{section}{\protect\numberline{\thesection}#1}% Add section to ToC
  }
  
\emergencystretch=1em

\title{OpenUAS:\\Third Semester Progress Report }
\author{ }
\begin{document}

%%TITLE PAGE%%
\maketitle

\newpage

%%TEAM PAGE%%
\begin{center}
\Large \textbf{The OpenUAS Team}

\vspace{1cm}

\large{
Abigail Gries\footnote[1]{ISU Department of Aerospace Engineering}\\ Logan Gross\footnotemark[1]\\ Madison Harrington\footnote[2]{ISU Department of Materials Science and Engineering}\\ Nick Hendrickson\footnotemark[1]\\ Chris Johannsen\footnotemark[1]\\ Jaymee Logan\footnotemark[1]\\ Jordan Reese\footnotemark[1]\\ Catherine Sener\footnotemark[1]\\ Alex VandeLoo\footnotemark[1]\\ Swathy Vidyadharan\footnote[3]{ISU Department of Mechanical Engineering}\\ Josh Wallin\footnote[4]{ISU Department of Electrical and Computer Engineering}\\ 
}\par

\end{center}

\newpage

%%TABLE OF CONTENTS%%

\tableofcontents

%%PROJECT OVERVIEW%%
\section{Project Overview}

\subsection{Purpose}
Currently, there are no open-source unmanned aerial systems (UAS) which are fixed-wing and conceptually available to the general public. There are some similar UAS which are available to the public, but they must be purchased and are not open-source. OpenUAS is producing an open-source, commercial off-the-shelf (COTS) UAS that can be used for recreational and research purposes, and it will only consist of components available to the general public, including open-source software.

\subsection{Scope}
In order to develop an open-source, COTS UAS for recreational and research purposes that is free and available to the general public, a list of objectives, deliverables, and constraints were identified at the conception of the project. The following section will provide an overview of these lists.

\subsection{Objectives}
\begin{enumerate}
\item Create an open-source, COTS UAS for short recreational and research flights
\item Provide full documentation of the conception, design, and testing of all systems
\item The UAS should not require a runway for takeoff or landing
\item The piloting of the UAS shall be accessible to hobbyists
\item The UAS shall be made of ``affordable" components
\item UAS components should be reconfigurable and support additional components
\end{enumerate}

\subsection{Deliverables}
\begin{enumerate}
\item A functioning design and prototype of a UAS
\item A ground launch system for takeoff
\item Relevant tools for piloting the UAS from the ground
\item Extensive documentation of the development process
\item Extensive documentation on proper use and safety
\end{enumerate}

\subsection{Constraints}
\begin{enumerate}
\item COTS components
\item Affordable components
\item Easily duplicated components (e.g. all 3D printed parts can be reasonably produced by hobbyists)
\item All components should be reasonably safe (e.g. battery)
\item Design and testing completed within 1 academic year
\end{enumerate}

%%BACKGROUND%%
\section{Background}

%%PROJECT DOCUMENTATION%%
\section{Project Documentation}

Varying forms of documentation were developed in order to assist with tracking the vision, objectives, high-level project plan, meeting documents to capture insight and actions needed, and so forth. The documentation is intended to not only support the systems engineering aspect of the project, but also serve an educational purpose by assisting future users who would like insight into what efforts and decisions were made to bring OpenUAS from a concept to a reality. Additionally, each individual on the team keeps their own weekly and semester progress documentation to maintain goals and the vision for every subgroup within the OpenUAS team. 

\begin{enumerate}
\item \textbf{Project Charter}\\ This is a one page document intended to help provide a broad overview of the project. The Project Charter lays out the team, the scope of the project, the purpose, and so forth. Additionally, the project objectives, deliverables, and constraints that were mentioned earlier in this paper come from the Project Charter as it maintains the vision and intent of the OpenUAS project.
\item \textbf{Weekly Meeting Agenda \& Minutes}\\Each week, Meeting Minutes are held to capture what discussion and decisions occurred. The tasks of leading the meeting and taking meeting minutes are rotated through the team. The one leading the meeting will set the agenda for that meeting's primary discussion points, and the meeting minutes are taken during the meeting on the shared Google Drive. Afterward, the meeting minutes are then cleaned up and formatted into the meeting minute document kept on GitHub.
\item \textbf{Requirements}\\ The requirements document is an extensive, volatile artifact that has been developed since the beginning of the project. Originally, our primary requirements were high-level, and directly traceable to the overall project goals. Now, as we begin to make decisions about what our design will look like, the requirements have evolved to become more detailed. For the sake of making requirements easier to read and understand, we chose to use the EARS \cite{Terzakis2013} requirements syntax.
\end{enumerate}

\section{Related Work}
\noindent Currently, there are very few comparable fixed-wing UAS. The United States uses UAS such as the RQ-14A Dragon Eye and RQ-11B Raven in its military. Although these UAS are similar in size and weight to the OpenUAS team's target design, the technology and capabilities of these systems are much more advanced, and as such, the budget well exceeds the team?s overall budget.\\

\noindent The University of Virginia created the Razor, a small fixed-wing UAS for the Department of Defense. This UAS has a flying wing design and utilizes an Android phone as the main processor. The Razor is of similar size, weight, and performance of the team?s target design. One main difference in this system is that it is entirely 3D printed. The team plans on utilizing 3D printing, but not to the extent of the Razor design.\\
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

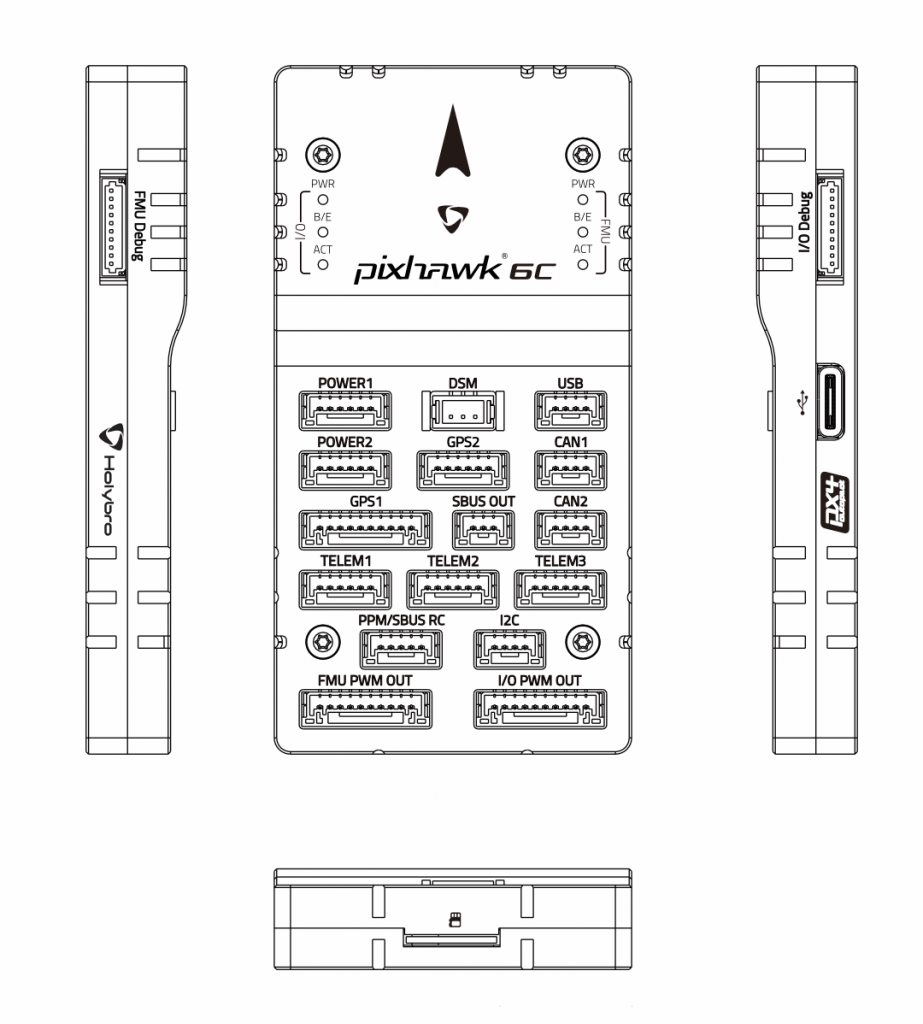
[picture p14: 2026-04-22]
docs/Pixhawk6C-Pinout-923x1024 (1).png

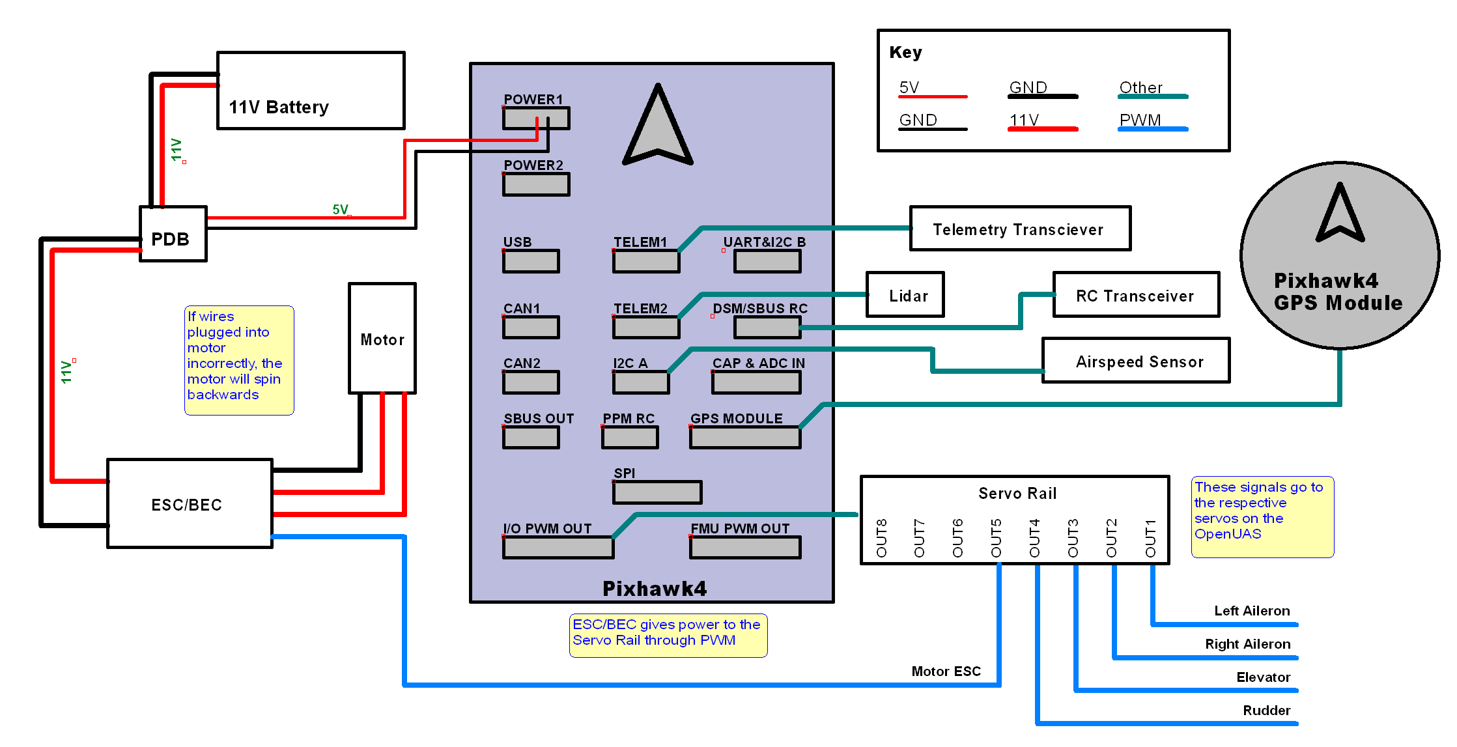
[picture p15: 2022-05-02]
docs/Electrical/openuas-electronics.png

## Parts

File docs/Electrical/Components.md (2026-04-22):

## Hardware Components

### [Flight Controller: Holybro Pixhawk 6c](https://holybro.com/products/pixhawk-6c)

- Dimensions: 84.8 x 44 x 12.4 mm
- Weight (plastic case): 34.6g

### [Flight Controller: Holybro Pixhawk 4](https://holybro.com/products/pixhawk-4)

We prefer using the more modern Holybro Pixhawk 6c.

- Dimensions: 44 x 84 x 12 mm
- Weight (plastic case): 33.3 grams

### [GPS: Holybro Pixhawk 4 Neo-M8N GPS](https://holybro.com/products/m8n-gps)

- Dimensions: 25 x 25 x 4 mm
- Weight: 32 grams

### [Power Module: Holybro APM Power Module 12S - PM02 V3](https://holybro.com/products/pm02-v3-12s-power-module)

- Dimensions: 18 x 23 mm
- Weight: 20 grams

### [Airspeed Sensor: Holybro Digital Air Speed Sensor](https://holybro.com/products/digital-air-speed-sensor-standard)

- Dimensions: (see below)
- Weight: 11.3398 grams

### [RC Transceiver: FrSky X8R 8/16ChS.Bus ACCST Telemetry Receiver W/Smart Port](https://hobbyking.com/en_us/frsky-x8r-8-16ch-s-bus-accst-telemetry-receiver-w-smart-port-no-antenna-cover.html)

- Dimensions: 46.5 x 27 x 14 mm
- Weight: 16.8 grams

### RC Controller: FrSky Taranis X9D plus

- (EXTERNAL TO UAS)

### [Telemetry Transceiver: Holybro 433Mhz 915Mhz Transceiver Radio Telemetry Set](https://shop.holybro.com/transceiver-telemetry-radio-set-v3_p1103.html)

- Dimensions: 28 x 53 x 10.7 mm (without antenna), 10 dia x 107 mm (antenna)
- Weight: 19.8447 grams

### [ESC: BadAss Renegade 85A ESC](https://badasspower.com/badass-renegade-series-brushless-esc-85a.html)

- Dimensions: 86mm x 33mm x 16 mm
- Weight: 91.6 grams

### [Motor: BadAss 2826-690Kv brushless motor](https://badasspower.com/badass-2826-690kv-brushless-motor.html)

- Dimensions: (see below)
- Weight: 180 grams

### [Propellor: APC 14x12 E](https://www.apcprop.com/product/14x12/)

- Dimensions: 355.6 mm long, 28.702 mm diameter round part, 17.018 mm thickness
- Weight: 64.35341749 grams

### [Battery: Ovonic 5000mAh 11.1V 3S 50C 3 Cell LiPo](https://www.amazon.com/5000mAh-Battery-Traxxas-Brushless-Spartan/dp/B07L6C7BX9)

- Dimensions: 155 mm x 43 mm x 25 mm
- Weight: 343 grams

### [Distance sensor (laser range finder): Lightware SF11/C](https://acroname.com/store/laser-range-sensor-r395-sf11-c)

- Dimensions: (see below)
- Weight: 35 grams

### Corona DS-239HV Digital Slim Wing Servo (Metal Gear)

- Dimensions: (see below)
- Weight: 22 grams
- [Corona DS-239HV Digital Slim Wing Servo (Metal Gear)](https://hobbyking.com/en_us/corona-ds-239hv-digital-slim-wing-servo-metal-gear-4-6kg-0-13sec-22g.html)

## Weights

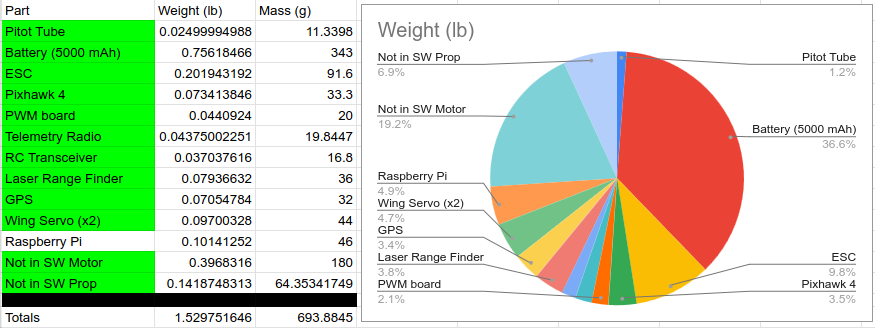
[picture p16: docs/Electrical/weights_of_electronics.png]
Weights of Electronics


## Wiring Diagram 

Wiring Diagram Current

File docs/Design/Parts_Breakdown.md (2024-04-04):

# OpenUAS 3.0 Parts Breakdown #

## 3D Printed Parts ##
### Fuselage ###
- (1x) - Fuselage-Tail Joiner (P-02)
- (2x) - Fuselage-Nose Joiner (P-04-02)
- (1x) - NoseCone_Front (P-01)
- (2x) - Wing_Rail (P-06-02)
- *(2x) - Fuselage_Top_Rail		(P-03-02)	{optional}*
- *(1-3x) - Fuselage_Rib				{optional}*
- (1x) - Front-Wing Mount (P-07)
- (1x) - Fuselage Bottom Rail_L (P-05)
- (1x) - Fuselage Bottom Rail_R (P-08)
- (1x) - Main Landing Gear Support_Inside (P-09)
- (2x) - Door Frame_Hinge   (P-10-02)
- (2x) - Door Frame_Inside  (P-11-02)
- (2x) - Door Frame_Outside   (P-12-02)
- *(1x) - Fuselage-Nose_Rail_BL			{optional}* (P-13)
- *(1x) - Fuselage-Nose_Rail_BR			{optional}* (P-14)
- *(1x) - Fuselage-Nose_Rail_TL			{optional}*  (P-15)
- *(1x) - Fuselage-Nose_Rail_TR			{optional}* (P-16)
- (1x) - Nose Drawer  (P-17)
### Tail ###
- (1x) - Updated_Tail_Feathers_Support_posterboard   (P-18)
## PosterBoard Parts ##
### Fuselage ###
- (1x) - Fuselage_Bottom (F-03)
- (1x) - Fuselage_Top (F-04)
- (1x) - Fuselage_Top_Front (F-05)
- (2x) - Fuselage_Sides (F-06-02)
- (2x) - Empennage_Sides (F-07-02)
- (1x) - Empennage_Top (F-08)
- (1x) - Empennage_Bottom (F-09)
- (2x) - NoseCone_Sides (F-10-02)
- (1x) - NoseCone_Top (F-11)
- (1x) - NoseCone_Bottom (F-12)
- (1x) - Tail_Bulkhead_Front (F-13)
- (1x) - Tail_Bulkhead_Middle (F-14)
- (1x) - Tail_Bulkhead_Rear (F-15)
- (2x) - Electronics Door Plate (F-16-02)
### Wing ###
- (2x) - USA35_inside_rib_posterboard (F-18-02)
- (4x) - USA35_middle_rib_posterboard (F-19-04)
- (4x) - USA35_outer_rib_posterboard (F-20-04)
- (2x) - USA35_posterboard (F-17-02)
- (2x) - Wing_Servo_Support (F-23-02)
- (2x) - Wing_Servo_Support_Rear (F-22-02)
- (2x) - Wing_Servo_Support2 (F-21-02)
### Tail ###
- (1x) - Vertical Stab_posterboard  (F-01 & F-01/2)
- (1x) - Horizontal Stab_posterboard  (F-02, F-02/2, F-02/3, F-02/4)
## Misc. Parts ##
### Fuselage ###
- (1x) - Motor Mount 
- (1x) - Propeller
- (2x) - Door Frame Hinge Rod 				{Carbon Fiber}
- (8x) - Rubber Bands for wing mounting			{Purchased}
### Wing ###
- (1x) - Front_Main_Spar_posterboard 			{Plywood or Balsa Wood} (W-04)
- (1x) - Rear_middle_Main_Spar_posterboard 		{Plywood or Balsa Wood} (W-01)
- (2x) - Rear_outer_Main_Spar_posterboard 		{Plywood or Balsa Wood} (W-02-02)
- (1x) - Rear_Spar_posterboard 				{Plywood or Balsa Wood} (W-03)
- (2x) - Ailerons 						{Balsa Wood}
- (6x) - Hinges						{Purchased}
### Landing Gear ###
- (3x) - Wheels						{Purchased}
- (1x) - Landing_Gear_Stock				{Purchased}
- (1x) - Landing Gear Bracket 
- (2x) - Axle						{Purchased}
- (2x) - Nosewheel Bracket				{Purchased}
- (1x) - Nosewheel Rod      {Purchased}
- (1x) - Nosewheel Horn     {Purchased}
## Electronics ##
- (4x) - Wing Servo {Thin Metal}
- (1x) - Pitot Tube 
- (1x) - Motor
- (1x) - Battery
- (1x) - GPS
- (1x) - Laser SF11
- (1x) - Pixhawk 4
- (1x) - Telementry Radio
- (1x) - RC Transceiver
- (1x) - ESC
- (1x) - Rasberry Pi 4 Model B

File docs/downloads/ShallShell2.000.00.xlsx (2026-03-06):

Level | ID | Name | Requirement | Parents | Children | Date | Status
1 | 1 | Fixed Wing UAS | System shall be a fixed wing UAS capable of takeoff, cruise flight, and landing. |  |  | 2026-02-22
1 | 2 | Autonomous Operation | System shall be capable of supporting autonomous operations, including navigation and stabilization functions. |  |  | 2026-02-19
1 | 3 | Comercial Off The Shelf | System shall be composed of exclusively Comericial/Off The Shelf (COTS) components. |  |  | 2026-02-19
1 | 4 | Cost | System shall be composed of materials cumulatively costing under $600. |  |  | 2026-02-19
1 | 5 | Flight Endurance | System shall have a minumum flight endurance of 15 minutes. |  |  | 2026-02-20
1 | 6 | Payload Volume | System shall be accomodate a payload volume of 7x5x4 in (17.8x12.7x10.2 cm). |  |  | 2026-02-19
1 | 7 | Payload Weight | System shall support a payload weighing 4 lb (1.81 kg). |  |  | 2026-02-19
1 | 8 | FAA Part 107 | System shall comply with all FAA Part 107 regulations. |  |  | 2026-02-19
1 | 9 | Reconfigurability | System shall support flight operations in more than 1 configuration. |  |  | 2026-02-19
1 | 10 | Reliability | System should be capable of achieving 1 flight per 18 man hours of assembly or maintainence effort. |  |  | 2026-02-19
1 | 11 | Reproducability | System shall be completely reproduceable with provided assembly and operation instructions. |  |  | 2026-02-19
1 | 12 | Storage Space | System shall include at least one configuration that fits within a storage volume of 12 cubic feet. |  |  | 2026-02-20
1 | 13 | ISU Policy | System shall comply with all Iowa State University Policies. |  |  | 2026-02-20
2 | 1.1 | Cruise Altitude | The system shall be capable of sustained cruise flight at altitudes between 350 ft and 400ft AGL | 1, 5, 8 |  | 2026-02-20
2 | 1.2 | Takeoff/Landing Length | The system shall be capable of completing takeoff and landing within a runaway length of 100 ft (30.48 m) or less. | 1 |  | 2026-02-20
2 | 1.3 | Control Surfaces | The system shall incorporate three primary control surfaces; elevator, aileron or flaperon, and rudder. | 1, 5 |  | 2026-02-22
2 | 1.4 | Taxi Controls | The system shall capable of ground taxi in a straight line within (+/-2 deg) of heading under its own power. | 1 |  | 2026-02-22
2 | 1.5 | Lift Capability | The system shall generate lift force exceeding its total weight during takoff, cruisem and landing phases. | 1 |  | 2026-02-22
2 | 2.1 | Telemetry | The system shall contain a COTS telemetry transmitter and receiver capable of sending and receiving data a direct distance of at least 1 mile. | 2, 8 |  | 2026-02-22
2 | 3.1 | Manufacturing System Cost | The manufacturing tools and systems required to construct the aircraft shall cost no more than $1000 in total. | 3, 11 |  | 2026-02-20
2 | 3.2 | Power Source | The system shall be powered by an electric battery as its sole onboard power source. | 3, 13 |  | 2026-02-20
2 | 4.1 | Manufacturing Cost | The total cost of aircraft structural components shall not exceed $100. | 4 |  | 2026-02-20
2 | 6.1 | Payload Orientation | The system shall support a payload with a maximum groundward facing area of 6x4 in (15.2x10.2 cm) | 6, 9 |  | 2026-02-20
2 | 7.1 | Weight | The system shall an empty weight not exceeding 13lb (5.9 kg) and a maximum takeoff weight not exceeding 17lb (7.1kg) | 7, 8 |  | 2026-02-20
2 | 8.1 | ADS-B Out | The System shall not include ADS-B Out or a Transponder | 8 |  | 2026-02-20
2 | 8.2 | Controller Type | The system shall utilize a COTS , Remote ID controller operating on non-aviation frequencies. | 8 |  | 2026-02-20
2 | 8.3 | Maximum Altitude | System shall not exceed a maximum altitude of 400 ft AGL during flight. | 8 |  | 2026-02-22
2 | 9.1 | Wing Reconfiguration | The wings shall removeable and re-attachable within 15 minutes to support reconfiguration and transport. | 9, 12 |  | 2026-02-20
2 | 12.1 | Transformation Time | The system shall be transformable from storage configuration to flight configuration in 15 minutes or less. | 12 |  | 2026-02-20

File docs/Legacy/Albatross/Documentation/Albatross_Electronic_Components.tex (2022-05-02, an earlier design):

\documentclass{article}
\usepackage[margin=1in]{geometry}

\linespread{0.3}

\begin{document}

\title{OpenUAS: Alabatross Electronic Components}

\author{Chris Johannsen}

\maketitle

\begin{enumerate}

\item Motor

\begin{enumerate}
\item Scorpion SII-4020-420KV\\
\end{enumerate}

\item ESC\\

\begin{enumerate}
\item Phoenix Edge 100A\\
\end{enumerate}

\item BECs\\

\begin{enumerate}
\item CC BED Pro 20A\\
\item Arris Swift 20A
\end{enumerate}

\item Battery\\

\begin{enumerate}
\item Graphene 8.0 Turnigy 22.2V 177.6 Wh 8000mAh 6S 15C\\
\end{enumerate}

\item Servos\\

\begin{enumerate}
\item HS-5065MG+\\
\item HS-5085MG+\\
\item HS-5245MG\\
\end{enumerate}

\item Long Range Radio\\

\begin{enumerate}
\item RFD 900+ Modem Ultra Long Range Radio\\
\end{enumerate}

\item FPV\\

\begin{enumerate}
\item DragonLink mini RF Module Full Range Receiver\\
\item DragonLink FPV\\
\end{enumerate}

\item Receiver\\

\begin{enumerate}
\item Albatross provided\\
\end{enumerate}

\item Camera\\

\begin{enumerate}
\item Albatross provided\\
\end{enumerate}

\item Sensors\\

\begin{enumerate}
\item On-Board Pixhawk\\
\begin{enumerate}
\item nvensense MPU 6000 Accelerometer/Gyroscope\\
\item ST Micro LSM303D Accelerometer/Magnetometer\\
\item ST Micro L3GD20H 16 Gyroscope\\
\item MEAS MS5611 Barometer\\
\end{enumerate}
\item Other Sensors\\
\begin{enumerate}
\item Paralax SF11-C 100M Laser Rangefinder\\
\item Cirocomm GPS module\\
\item Goodluckbuy.com PX4 Airspeed Sensor\\
\end{enumerate}
\end{enumerate}

\item Digital Telemetry System\\

\begin{enumerate}
\item Taranis X9D Plus\\
\end{enumerate}

\end{enumerate}

\end{document}

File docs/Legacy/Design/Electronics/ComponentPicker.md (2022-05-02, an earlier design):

# Battery
Provides power to the system.

Specs:
* mAh - Milliamp Hours
  * Describes how much energy the battery contains. Higher mAh usually means it can power the system for a longer time.
* C - Discharge
  * Current that the voltage can be discharged at.
* V - Voltage
  * Voltage supplied from the battery

https://web.mit.edu/evt/summary_battery_specifications.pdf

Common Issues / Solutions:
* Short Flight time
  * Increase the mAh
* ...

# Electronic Speed Controller (ESC)
Used to control the motor. Powered from the 12 V line. Accepts input as PWM from the pixhawk in order to control the speed the motor runs at. Will want an ESC that also has a BEC so that it can power the servo rail.

Specs:
* Continuous Current -
  * The max current that the ESC can continuously handle. Should be rated for the maximum amps that the motor can pull.
* Burst Current -
  * Current that the ESC can handle for short amounts of time (~10 seconds)

https://oscarliang.com/choose-esc-racing-drones/

Common Issues / Solutions:
* ...
  * ...

# Battery Eliminator Circuit (BEC)
Used to drop voltage, in this case from 12 V to 5 V. Power goes in from the 12 V and out to power the servos / PDB / anything else that would need 5 V. These external BECs are used for LiPo Batteries of about 3S or less.

Specs:
* Amps
  * This corresponds to how much amperage the BEC can deliver to whatever it is connected to. The more servos or other things trying to be run, the higher rated BEC you will want.

https://www.dimensionengineering.com/info/bec

Common Issues / Solutions:
* ...
  * ...

# Power Distribution Board (PDB)
Used to send power to different parts of the circuit and stand as a safety net. Contains a fuse that would burn out the chip before damaging the rest of the system. Powered from the 5 V line from the BEC. Has the 12 V line run through it to monitor the power. Sends power to the Pixhawk.

The main purpose of our PDB seems to be to convert the power so we can power the pixhawk. I would jut suggest choosing the one that would come along with the pixhawk.

Specs:
* ...

Common Issues / Solutions:
* ...
  * ...

# Motor
Provides the thrust for the UAS.

Specs:
* ...

Common Issues / Solutions:
* ...
  * ...

# Propellor
Contibutes to the thrust of the UAS

Specs:
* ...

Common Issues / Solutions:
* ...
  * ...

List:
* What each part does
* How it works?
* What do the part specs mean
* What are common problems that can be fixed by chnging these specs
* What would changing this component also impact

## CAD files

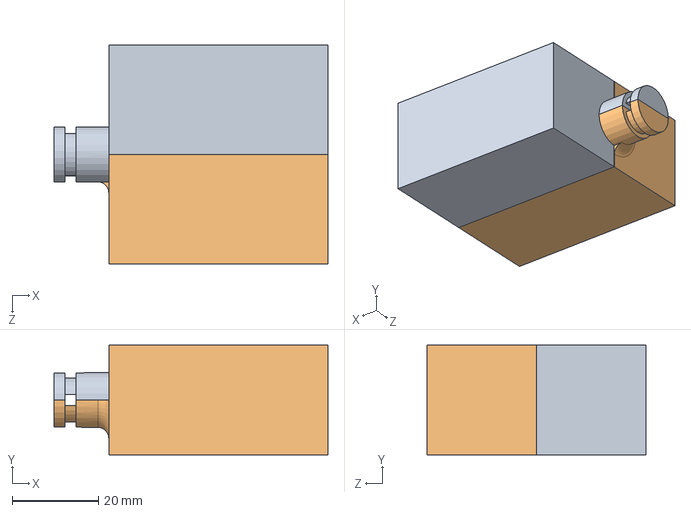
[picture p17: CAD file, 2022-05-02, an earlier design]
docs/Legacy/Archive/3D_Printed_UAS/Parts/Connectors_Test_OpenUAS.SLDASM
63.5 x 25.4 x 50.8 mm
Connector Female
Connector Male

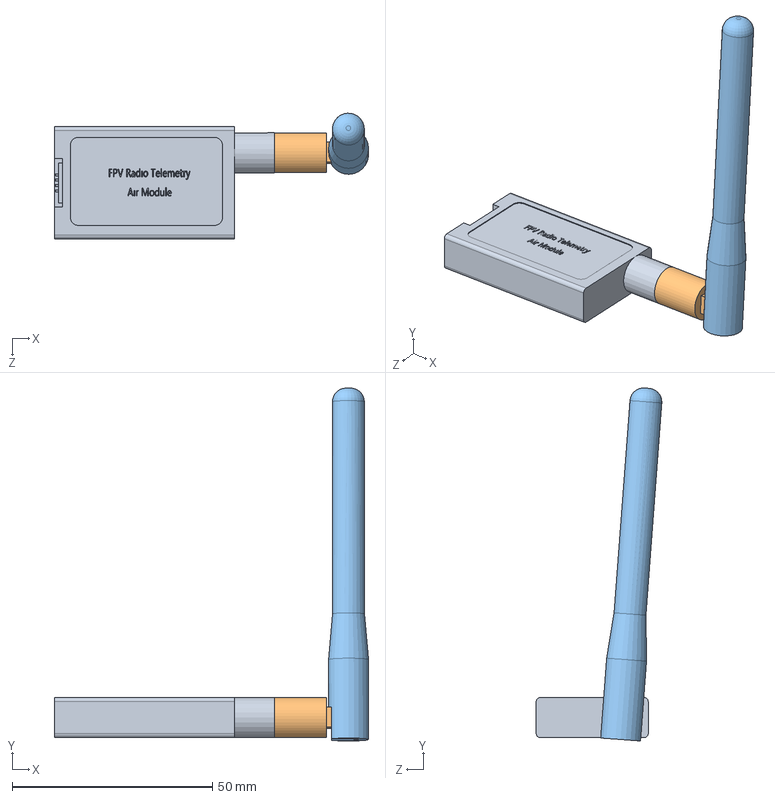
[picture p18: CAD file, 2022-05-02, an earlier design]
docs/Legacy/Archive/Electronics/wiring-archive/IronBird_V2/Telemetry/Telemetry.SLDASM
78.5 x 88.2 x 31.4 mm
baseTel
connector
antena

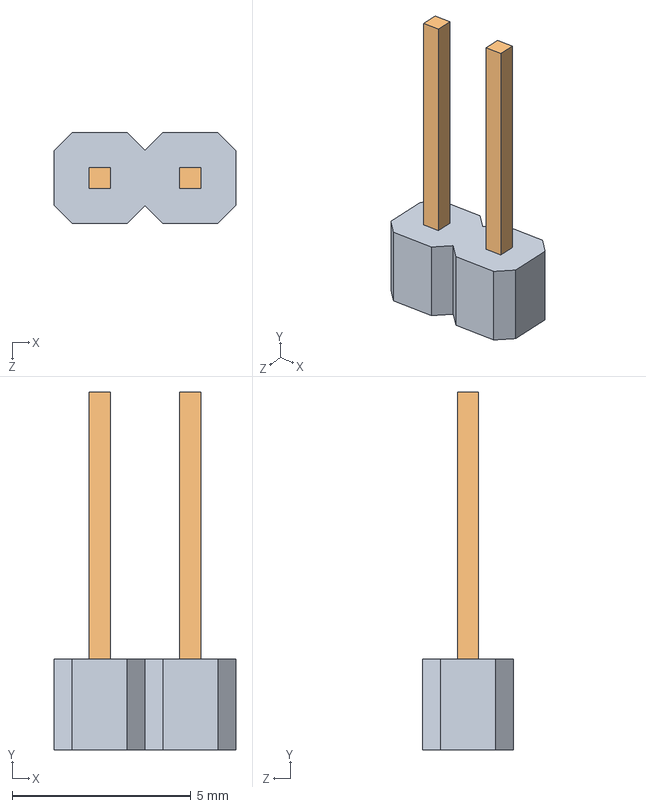
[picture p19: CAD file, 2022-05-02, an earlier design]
docs/Legacy/Archive/Electronics/wiring-archive/IronBird_V2/X8R/Pin2_asem.SLDASM
5.08 x 10.0 x 2.54 mm
pin_body
Pin x 2

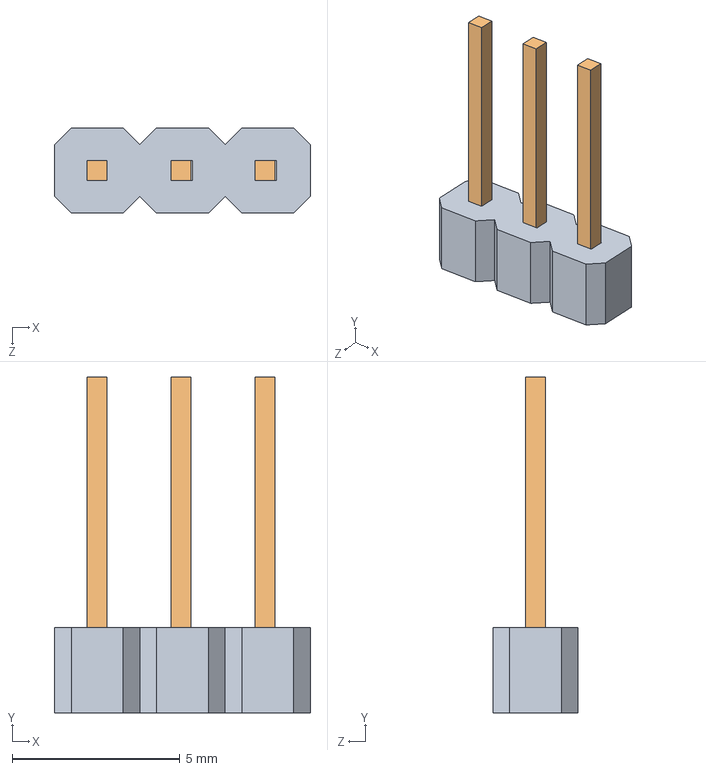
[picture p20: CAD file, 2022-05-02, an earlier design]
docs/Legacy/Archive/Electronics/wiring-archive/IronBird_V2/X8R/Pin3_asem.SLDASM
7.62 x 10.0 x 2.54 mm
pin_body3
Pin x 3

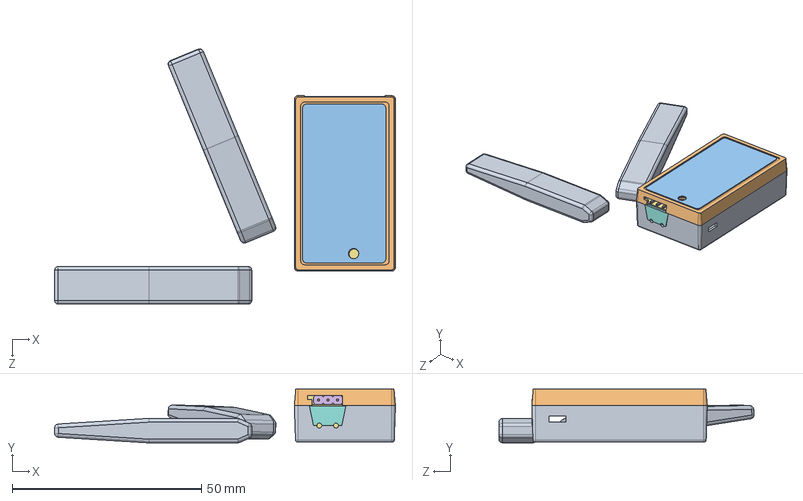
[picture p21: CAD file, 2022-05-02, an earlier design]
docs/Legacy/Archive/Electronics/wiring-archive/IronBird_V2/X8R/X8R (1).SLDASM
90.2 x 14.2 x 67.6 mm
X8R_body_down
X8R_body_up
Etiket
pin_body x 12
Pin x 33
pin_body3 x 3
plate x 2
cap
Patch_antena x 2

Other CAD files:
docs/Legacy/Archive/3D_Printed_UAS/Parts/Connector_Male.SLDPRT
docs/Legacy/Archive/Electronics/wiring-archive/IronBird_V2/BEC.SLDPRT
docs/Legacy/Archive/Electronics/wiring-archive/IronBird_V2/Telemetry/baseTel.SLDPRT
docs/Legacy/Archive/Electronics/wiring-archive/IronBird_V2/X8R/pin_body.SLDPRT
docs/Legacy/Design/Electronics/Open UAS Parts/Switch (for Open UAS ESC).SLDPRT
docs/Legacy/Archive/3D_Printed_UAS/Parts/Connector_Female.SLDPRT
docs/Legacy/Archive/Electronics/wiring-archive/IronBird_V2/ESC.SLDPRT
docs/Legacy/Archive/Electronics/wiring-archive/IronBird_V2/Telemetry/connector.SLDPRT
docs/Legacy/Archive/Electronics/wiring-archive/IronBird_V2/X8R/Patch_antena.SLDPRT
docs/Legacy/Design/Electronics/Open UAS Parts/Big Thruster.SLDPRT
docs/Legacy/Archive/Electronics/wiring-archive/IronBird_V2/Battery.SLDPRT
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

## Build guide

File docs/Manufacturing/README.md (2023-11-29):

# Manufacturing

The OpenUAS 3.0 is designed to be an easy build for those with minimum manufacturing experience and resources. This page serves as a quick reference that includes the time commitment, manufacturing tool requirements, and price expectations. 

| Task | Time Expectation |
|---|---|
| Fabrication Time by Hand | 3 hours |
| Fabrication Time by Laser Cutter | 1 hour |
| 3D Print Time | 30 hours |
| Assembly Time with 4 people | 5-10 hours |

## Tools Required:
- Dremel
  - Dremel Rotary Tool Accessory Kit- 710-08-160
    - Carving/Engraving 191
    - Sanding 407
    - Cutting EZ476 
- EXacto Knife/Box Cutter
- Large Straight Edge (24+")
- Small Straight Edge (6")
- Small Screwdrivers
- Drill
  - Phillip Driver
  - 3/16" bit
- 3D Printer

## Building Materials:
- PLA Polylite
- Poasterboard (qt 5, 22"x28")
- 1/8" Rods

## Adhesives and Fasteners:
- Hot Glue
- Super Glue
- Packing Tape
- 2 Part Epoxy

## Airplane Hardware:
- Du-Bro Super Strength Landing Gear
- Du-Bro Steerable Nose Gear (Straight)
- Du-Bro Super Slim Lite Wheels (3")
- Magnets (1/8")
- Servos
- Pushrods
- Servo Horns
- Hinges
- Electronics

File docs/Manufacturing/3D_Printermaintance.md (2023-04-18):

## Maintenance for the 3D printer

Summary table for quick refernce :
| Part | How often it should be cleaned | How to clean it| 
| :---: | :---: | :---: |
| Rods | Before every print | Wipe with a clean paper towel. DO NOT USE A CHEMICAL CLEANER OF ANY KIND!!!!!| 
| Printing bed | Before every print | Wipe with a wet paper towel. Only use soap and water on a towel if glue was previously used on the bed and remains on the surface. |
| Flash Drive | Every Semester (approx 16-20 weeks) | Plug into the USB port on the laptop from here there are two methods. 1. Manually remove the files from the files tab 2. Right click the device in the files tab and select format, then quick format to remove everything on the flashdrive. \* For mac please look up instructions|
| Environment | Monthly | Move the printer to a different location and wipe down the counter and dust surrounding the area. Replace printer to location. \*Remember to unplug the printer when moving it |
| Calibration of Printer head (simple)| Once to twice a year or as needed if issues arise | First step to go directly to the printer settings, Select advance settings, Select Nozzle offset,(before the next step be sure to record important settings refernce below for how and what to save before cailbrating) Select AutoMeasure. Make sure there isn't anything that would get in the way of the printer head and let it do it's thing. In some case it make take more than one try to correctly calibrate the printer head. | 
| Calibration of Printer (Complex) | As needed. Usually when issues such as lopsided holes, non-squared edges and layers appearing skewed. | First step is to print a calibration square and measure the offset from perfect angles/holes. Then going into the gcode in Cura we can adjust the x, y and z axis distance and complete a reprint of the same calibration square. I recommend refering to the documention of the calibration square you choose to you. | 
| Adjustment of z-offset| As needed. Is needed When the printer head is too close or too far from the printing bed. (signs include poor bed adhesion, flatened printed filament, consitant clogging of the nozzle, or head running into the bed itself) | This process is itertive in naturate and starts with first going into the printer menu, selecting advance settings, and then selecting z offset. From here it is good to note what the z offset is currenlty at as this will be your starting point. Other notes the z offset should be a negtive number, it is recommend any changes made are done in increments of .01mm which is NOT the default setting and will have to be selected, the more negtive the number the further the head will be set from the bed (in other words closer to zero closer to the bed). Adjust as needed with good judgement and try a new print. Be sure to watch as it gets close to the bed and readjust as needed for the head to ensure the head is where it needs to be. |  

## General use 

Before using the printer, a few things should be cleaned and checked before beginning the print. The biggest and most important part of regular maintenance for the printer is making sure the rods are dust free. A big note for the printer rods is that they are used by the self-lubricating bearing that connects the printer head and bed to the rest of the printer. This is important because if you add a cleaner that is unsafe for the bearing, you will cut the printer's lifespan significantly. 

With this in mind, the first maintenance step before each print is to take a clean paper towel and wipe the rods as is. DO NOT add cleaner (Including soap and water) or use a disinfectant wipe; this will cause damage to the bearings and, therefore, the printer. In many cases, black/ gray dirt may come off the rods. That's okay; that is why we are wiping them down; if we do not remove the dirt, it will build up and create a squeaking noise (otherwise described as cat screeching). If it does get to this point, it will take a few times to wipe off the rods before the noise stops.

For the printing bed, the prep is a little different. Depending on what material you are printing with, it will depend on how you prep it, but the most common way is to wipe the bed down with a wet paper towel to remove any dirt on the bed. If the last print you did needs to be glued onto the bed, it is recommended to wipe the bed down with a soapy paper towel until the glue is completely removed, then dry the bed afterward. Depending on the material you are printing with, it might change, but currently, for the materials in the lab, you then wipe the bed down with a 93% alcohol solution that can be applied with a paper towel (not the one you cleaned it with). 

## Caibration 

Every so often there is the possiblity of the cailbration being a bit off on the printer espically if the printer is being fequently in a short time span. There are a few different ways to go about this depending on the needs of the printer. If it is just a small issue the printer has it own cailbration setting under the menu tab in advance settings. Before Cailbrating you should record a few different settings as they can be reset during the cailbration process and will need to be manually reinputed to the printer. These Include the z offset (has its own tab in advance settings), E steps, X steps, Y steps, and Z steps (E, X, Y, Z steps are all under the Steps/mm tab in advance settings). 

Once you have the information on the settings written down we can then go back to the advance settings tab and then select the Nozzle offset tab.Then select automatically measure. This will start the cailbration process and you need to make sure nothing is blocking the path of the printer head and wait for the printer to stop. Repeat the process as needed and then check the z offset, E steps, X steps, Y steps, and Z steps and reinput them if needed. 

## Z offset

The z offset on the printer is important to know and adjust as needed. This setting is respondable for how far/close the head is to the bed to the printing bed. There are a few different ways of going about determining the needed offset however, the one described in the above summary table is the most straightforward and least complex method. Please remeber to start slow and not make large jumps in the z offset as it can result in damage to the printing bed.  

Over time the z offset will shift due to a varity of different reasons and is something to watch out for. If there is a big and sudden shift in the z offset I recommend doing a printer cailbration first and then adjusting the z offset. This should help you get closer to the desired z offset in a shorter time period. In most cases it will also fix other issues that are occuring during printing such as lop sided holes or skewd edges.

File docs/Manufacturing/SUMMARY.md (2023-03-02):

# Summary

* [Manufacturing](README.md)
* [3D Printer Settings](3D_Printer_Settings.md)
* [Cura Setup](CuraSetup.md)
* [Printer maintance](3D_Printermaintance.md)
* [Poster Board Arrangement](PosterBoardArrangement.md)

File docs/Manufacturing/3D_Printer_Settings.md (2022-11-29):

# 3D printer settings:

The following are the settings that we found successful when printing various parts in PLA and ABS.

## PLA (Polymaker 2.85mm)
- Nozzle temp: 220&deg;C
- Bed temp: 45&deg;C
- Probe Temp: 190&deg;C
- Soften Temp: 190&deg;C
- Wipe Temp: 190deg&C
- Final Print Temp: 200&deg;C
- Part Removal Temp: 40&deg;C
- Print Speed: 45mm/s

## ABS (Polymaker 2.85mm)
- Printing Temp:  250&deg;C
- Build Plate Temp: 90&deg;C
- Probe Temp: 160&deg;C
- Soften Temp: 170&deg;C
- Wipe Temp: 240&deg;C
- Final Print Temp: 240&deg;C
- Part Removal Temp: 90&deg;C
- Print Speed: 45mm/s

## PolyDissolve S1 (polymaker 2.85mm)
- Printing Temp: 215-225&deg;C
- Build plate Temp: 25-60&deg;C
- Probe Temp: 190&deg;C
- Soften Temp: 190&deg;C
- Printing Speed: 30-40mm/s
- SUPER IMPORTANT DO NOT USE WITH ABS 
- Compatable material types include : PLA, TPU, PVB, and Nylon

## The Use of Settings to improve the quailty of a print
3D printers have a variety of applications that can be useful for several reasons. This document will cover some basic and helpful settings for 
ensuring a quality print for different needs. Please note that the settings gone over in this section are not related to print mature and or material type, and these settings should be checked before any other troubleshooting is done. Please refer to the 3D printing settings sections under the Manufacturing documentation if you want this information. 

# Bed Adhesion settings 
One of the most important part of ensuring a qutily print from a 3D printer is to ensure the bed adhesion settings are set to match the needs of the part being printed. 
There are 3 differnet settings that can be selected for the bed adhesion that are helpful for different part types. 

Bed Adhesion types
* Skirt
* Brim 
* Raft 
* None \* Technically not a type but is an option 

# Skirt 
The skirt setting in Cura Lulzbot Edition is simple to use and what it does is create a line around the part before printing the part. This is useful in some cases if 
the printer has poor material flow issues. It is not commonly used for many parts unless the part is larger and is printed to a higher/fine quality to ensure the material flows smoothly. 

# Brim 
More commonly used than the skirt setting, the brim setting is reserved for odd-shaped or larger prints. The brim is a layer of filament that creates a larger adhesive surface that is better for holding onto the part. In other words, the part has less of a chance of being pulled off the build plate midpoint. For more of the odd-shaped prints, this helps ensure the print layers are smoother at the start of the print and will match the quality of the final layers.   
It does use a decent amount of filament during printing and is more of a waste of material for smaller prints, so using a brim in those cases would not be the best option unless all other options for diagnosing the problem have been addressed. 

# Raft
A raft is infrequently used for parts. This setting works best for smaller parts that do not have a "good" amount of adhesive surface connected to the build plate. This leads to the part being pulled off the build plate early in print and, in some cases, can cause damage to the nozzle from clogging. 

# None 
This setting is more used for prints where you would use a skirt; however, you are not having problems with the flow of the filament; therefore, using a skirt is unnecessary. In many cases, this is the best option to limit filament waste. This is also an acceptable bed adhesion setting if the print quality is lower, as it does not assist or take away from the print quality. 

\* In some cases, using a **light** layer of glue on the print bed can eliminate the need for adjustments in the bed adhesion settings. Please note that this method does require the user to clean the bed before and after the print takes place to help ensure the print bed is smooth for printing. 

# **Other Helpful Settings/Actions for Bed adhesion** 
The bed adhesion can be affected by several external factors and the g code settings set by the slicer. These external factors result from the environment in which the printer is stationed to print. In the case of the lab, we know that a draft affects the quality of the prints we get regardless of the settings we use in Cura Lulzbot Edition. The draft creates an issue with the layers being smooth when the print is completed due to inconsistent cooling time. A newer setting released by Cura Lulzbot Edition is the experimental setting referred to as *Enable Draft Shield* Which then brings up a range of different settings, including the distance from the print it is along with the height of the shield.

This setting can be useful in spaces like the lab where a small draft affects the print, even with a printer shield. It does use a lot of material to create the shield, so if used, try to limit the excess nature of the setting. This can include shorting the default height or bringing the shield closer to the print. Another solution to this issue is to run a few tester prints with different fan speeds to determine if the fan adds to the problem. This method is more time-consuming, but if the problem is consistent across different prints, this may be a better long-term solution to prevent warping and the part from coming off the printing bed. 

## Support Generation 
It is not uncommon for a part to need support material to turn out correctly and to a high standard. Cura is great at automatically generating support material for imported files. However, there are some cases where the settings will need to be adjusted to meet the needs of the part.

The Support Tab is one of the main Tabs in the right-hand menu. All of the settings under this tab can be found through the search bar after typing Generate Support. Most settings relate to which head is used to create the support. A general rule for this is if you are using the same material for the support, then you only need the Hot End 1; if you a using a different material for support, then Hot End 2 should be selected. 

# Support Placement
The support placement is one of the more useful setting that will change the most. It has two options that include 
* Touching Build plate 
* Everywhere

The Touching Build Plate setting is useful in two big ways. One, it reduces the amount of filament used for the supports. Two, it helps to keep the support filament in areas the part needs instead of every gap. At the end of the print, this is helpful for removing the support material from the print without damaging the part or causing harm to anyone trying to remove the part. 

The Everywhere setting is one you need to be careful with, as it is the default setting and is meant for less complex parts that need some support. If you are using dissolvable filament, this setting is less of an issue, but for most cases in the lab, we use the same material, making it dufficult to remove the part.

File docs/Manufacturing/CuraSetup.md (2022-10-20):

# What Slicer do we use? 
Our 3D printer is a Lulzbot Taz Pro for the Lab, and we use the Cura Lulzbot Edition as our Slicer. 

## How to get started with Cura Lulzbot Edition 
Cura is a free-to-use slicer that requires no special operating system or hardware. From any search engine, you should be able to look up Cura Lulzbot 
Edition and download the respective software for the operating system on your device (laptop/desktop). It should not take an extended period to download the
software after following the instructions provided and installing it on the Cura website (https://lulzbot.com/support/cura).   

Once Cura Has been installed and opened, you should see an opening screen asking you to set up the printer. For the case of the Lab, our setup is the Lulzbot Taz 
Pro with dual head extruders. After setting up the printer on your device, the next important step before printing is ensuring that you have the correct material 
selected with the corresponding settings. 

In order to select the material, you need to view the right-hand menu, which has various options for the settings in Cura. We want to look 
at the second option from the top of the menu bar. There should be a drop-down menu with a preset list of materials that can be chosen from. In the Lab, we have a few different 
materials we use for printing, but our most common is the Polylite PLA which Polymaker produces. For more information on the generic settings for PLA please refer to the OpenUAS Website section 3D printer settings tab under the manufacturing section. 

\* Will show up as PolyLite PLA (Polymaker) in the material section 

Suppose the material you are using is not listed. In that case, you can use the information from the material data sheet 
that gives recommended setting provided by the manufacturer and create a custom material under the custom 
tab in the drop-down menu. More instructions on how to do that will be located later in the documentation. 

I recommend taking a few minutes to review the settings, particularly the temperature settings, to ensure they match the recommended 
levels from the manufacturer. There are general temperatures for the materials; however, the manufacturer's recommendations
tend to work the best to insure the quailty of parts. You can do this by scrolling through the print setup settings, selecting the custom tab, and using the search bar to look up keywords for the desired setting. 

\* For example, type printing temperature to see the printing temperature-related settings. 

This is the standard setup of the Cura Lulzbot edition. From this point, you should be able to open an STL file of a model and print. There are more specialized settings for different types of parts that can be used but are more in depth and will be revised in another document.

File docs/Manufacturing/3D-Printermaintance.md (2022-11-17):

# When to do Maintance on the Lulzbot Taz Pro

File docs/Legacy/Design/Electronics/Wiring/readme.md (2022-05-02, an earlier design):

#  Power System Wiring
Power system wiring
## Component Descriptions

* __**Battery:**__ 
The battery supplies the power to the system. The Iron Bird uses a 12 volt 3 cell battery.<br />
* __**Power Distribution Board (PDB):**__ 
The power Distribution board splits the power into two lines, a 5v line that goes to the pixhawk, and a 12v line that powers the ESC.<br />
* __**ESC:**__ The current iteration ironbird uses the Badass Renegade 85A ESC. The ESC provides power and control to the motor. The Renegade also has a built in Battery Elimination Circuit or ESC, which drops the voltage to 5v can be wired to the servo rail and power the servos.<br /> 
# Control System Wiring
Control system wiring
A more in depth explanation about wiring the pixhawk 4 can be found on the pixhawk website, [here](https://docs.px4.io/v1.9.0/en/assembly/quick_start_pixhawk4.html).<br />
## Component Descriptions
* __**Tranceiver:**__
The tranceiver set allows the pixhawk to communicate with the ground station.<br />
* __**Servo Rail**__
A used to distribute power and PWM signal to each servo on the Iron Bird. The power comes from the ESC while PWM signal is sent from the Pixhawk4.

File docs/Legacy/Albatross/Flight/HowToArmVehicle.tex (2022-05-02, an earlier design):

\documentclass[a4paper]{article}

\usepackage[english]{babel}
\usepackage[utf8]{inputenc}
\usepackage{amsmath}
\usepackage{graphicx}
\usepackage[colorinlistoftodos]{todonotes}

\title{How to start Albatross}

\date{\today}

\begin{document}
\maketitle

\begin{enumerate}

\item Make sure all peripherals are plugged in to Pixhawk.
\item Plug in battery

	\begin{itemize}
	\item Make sure Pixhawk light is not red, that means there is an error
	\item Keep in mind if you do have an error, you can always plug in the Pixhawk to your computer and view the error message
	\end{itemize}

\item Turn on Taranis controller. The light on receiver should turn blue
\item Hold button on the side of Albatross until a noise plays.

	\begin{itemize}
	\item If Pixhawk flashes red, an error occurred
	\end{itemize}
	
\item Move the joysticks to make sure servos are now on
\item Hold throttle joystick to bottom right until a noise plays

	\begin{itemize}
	\item Should be a low pitch solid buzz, if not an error occurred
	\end{itemize}
	
\item Motor is now armed, the craft should be ready to go

\end{enumerate}

\end{document}

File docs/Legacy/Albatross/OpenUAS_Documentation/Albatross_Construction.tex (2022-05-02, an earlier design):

\documentclass{article}
\usepackage[margin=1in]{geometry}
\usepackage{graphicx}
\graphicspath{ {ConstructionPics/} }

\begin{document}
\title{\bf Applied Aeronautics \& OpenUAS: Albatross Construction Instructions and Notes}
\author{Madison Harrington}
\maketitle

\textbf{Contents}
\begin{enumerate}
\item Safety Considerations
\item Propellor
\item Servos
\item Lidar and GPS
\item Airspeed Sensor
\item Telemetry
\item Avionics 
\item Conclusions \newline
\end{enumerate}
The OpenUAS team followed the instruction provided by Applied Aeronautics for the majority of the construction of the Albatross UAV, but there were some minor adjustments to the procedure that are noted in detail in this document. All images were taken by OpenUAS team members.
Applied Aeronautics has a useful file for 3D prints, miscellaneous photos, and some instruction:

\ \

https://files.appliedaeronautics.com/Login \newline
Login: aacustomer \newline
Password: endurance \newline

\ \ 
\clearpage
\section{Safety Considerations}

It is recommended to wear a mask, safety goggles and keep the room in use ventilated while drilling into the Albatross. Spraying the surface with water before drilling is also recommended to mitigate the dust and cracks in the paint. \newline
\clearpage

\section{Propellor} 
Included in this section are steps in how our OpenUAS team assembled the propellor and images of the process. The propellor from the Applied Aeronautics kit did not fit on the screw assembly that they instructed to make. Therefore, the propellor's hole was increased to allow the assembly. The assembly was made to mimic the Applied Aeronautics' instructions, though some of the pieces did not match their kit so there was also some improvisation in the layers.

\begin{enumerate}

\item On the propellor, use a dremel to allow the screw to fit through propellor. Be careful to make an even and circular shape and to only increase the diameter as needed to fit on to the mount. Make small changes with the dremel and frequently check the fit to the mount's screw.
\item Layer all the pieces together as shown in the images below. The circular disk should be on bottom with the screw through that. Use the two washers on top of the large circular disk, then the propellor, and a nut on top of that. Ensure that everything is very secure. 
\item Choose the smallest screw from the kit (or the largest that fits to the bottom of the large screw). This will be placed through the nose cap along with a small nut and into the large screw to secure the nose cap to the rest of the pieces. Ensure this is tightened well.
\end{enumerate}

\begin{center}
 \newline
Here you can see the screw fitting into the circular disk. \newline
 \newline
Here you can see the internal assembly outlined in step 2 above. \newline
 \newline
 \newline
Note here the hole in the top of the screw, this is where the screw through the nose cap screws into. \newline
 \newline
Above you can see the final assembly, with the cap on the propellor and the screw through the top of the nose cap secured to the assembly. \newline


\end{center}

\clearpage
\section{Servos}

\subsection{Nose Wheel Servo}

\begin{center}

\end{center}

\clearpage
\subsection{Servo Holders}
   \begin {enumerate}
   \item Using the 3 3D print files for servo holders in the documentation. Print (with PLA filament):
   	\begin{itemize} 
	\item 3 HS-5085 holders
	\item 2 HS-5085 holders
	\item 2 HS-5245 holders 
	\end{itemize}
   \item Ensure that the servos snap nicely into the holders. 
   \item Use the softer side of the velcro sheets and stick these on the back of the servo holders. Use scissors and/or an exacto knife to cut these out.
   \end{enumerate}
   
\subsection{Servos}
   \begin{enumerate}
   \item *information regarding servo heads and screws*
   \end{enumerate}

\subsection{Servo connectors}
The servo connectors use 2 mm screws, a washer between the control surface and the first nut, then a nut underneath and on top of the joint link. There are three nuts total. (See the images at the end of this section)
\begin{enumerate}
\item Ensure that all the proper screws, washers and joint links are available as shown in the pictures. 
\item Using the $\frac{3}{32}$ inch drill, drill into the preset holes on each of the control surfaces (six in total).
\item Within the servo chamber, place one half of the velcro along the entire floor so that the servo can be positioned wherever desired. The back of the servo holders should have the opposite side of the velcro adhered to it. The servo can be screwed into the servo holder to minimize movement. 
\item Also be careful in how the servo is oriented when placed in the little groove. The white servo head should be free to move in the direction only away from the wing; so if it is sitting in the holder, the servo head should not move on the side of the holder. The head should also on the control-surface side of the servo chamber in order to make the joint-link connect to the control surface correctly.
\item Match the servo-joint link for matching control surfaces. The ailerons' joint links should be the same length so that inputs will actually match on both sides. This should be done for the flaps and rear controls as well.
\item Don't worry about which way the wires are facing in the servo chamber; the most important thing is to get the servo connected to the control surface, and secured. 
\item Once the servo is in place, use styrofoam or some sort of soft material to adhere to the inside of the servo cover (the white piece that screws over the servo hole). This is to compress the servo and mitigate any sort of movement against the velcro that it is sitting on. The cover should fit somewhat tightly once screwed in, just be careful not to add too much cushioning so that the screws are over stressed.
\item 
\end{enumerate}

\subsection{Aileron Servos}
You'll notice here construction completed as instructed by Applied Aeronautics: \newline

\begin{center}

\end{center}

   Reference the following pictures.
   \newline
   
   \begin{center}
    \newline
    \newline
    \newline
    \newline
   \newline
   \end{center}
\clearpage

\section{Lidar and GPS}

\begin{enumerate}
\item Print the Lidar Stencil (from the Applied Aeronautics 3D print files) 
\item Unscrew and remove the rectangular carbon fiber tray from inside the fuselage. This should reveal the bottom of the fuselage for easy drilling. 
\item Place the 3D printed Lidar stencil in the fuselage approximately 3cm from the front edge of vertical carbon fiber brace.
\item Trace the outside of the stencil on the inside of the fuselage. Use a needle tool to poke through the fuselage in both holes with the given holes in the stencil. This represents the center of each lens. 
   \begin{itemize}
   \item NOTE: Be sure to pierce all the way through the skin of the fuselage.
   \end{itemize}
\item Flip the fuselage upside down (bottom facing up).
\item Align the stencil with the same holes just punctured and trace the outline of the lidar stencil. 
\item Using the two pin holes as a guide, drill two 19mm holes centered at these pin holes.
   \begin{itemize}
   \item NOTE: We recommend drilling smaller holes such as $\frac{5}{8}$ inches then using a dremel to fill in the stencil?s outline. This is to        be done with caution, doing fittings of the lidar in between dremeling.
   \end{itemize}
\end{enumerate}

\begin{center}

\end{center}

\clearpage

\section{Airspeed Sensor}

\begin{enumerate}
\item The airspeed sensor should stick out of the front of the Albatross like a Narwhal. Use a flashlight and note the white crease of the front of the inside of the nose.
\item Lay the airspeed sensor flat on the internal shelving and mark a hole at the point of the inside of the nose where you intend to drill.
\item Using your fingers, estimate where the hole will lead to the outside of the fuselage. 
   \begin{itemize}
   \item NOTE: There is no good way to drill the hole, so estimate as best as possible from the outside.
   \end{itemize}
\item Drill small hole where you marked, directly into the front of the nose of the Albatross (this hole should be above the point of the nose) parallel to the longitudinal axis of the fuselage. 
\item Compare this small hole to the mark on the inside of the fuselage and adjust as necessary. 
\item Slowly drill a 4mm hole parallel to the longitudinal axis of the fuselage. Check to see if the airspeed sensor fits in this hole. 
\end{enumerate}

\begin{center}

\end{center}

\clearpage

\section{Telemetry}

\subsection{Drilling}
Holes will be needed on the panels that cover the telemetry on the Albatross. The recommended procedure for doing this is as follows:
\begin{enumerate}
\item Trace out the telemetry unit (the black grid and two antenna) so that the antenna fit in the storage area on the body part of the Albatross wing. There should be a hole so the square grid can face the open air for cooling purposes. The two antenna will also need holes through the panel so trace small circles where they align with the square drill site. Be careful to leave adequate room for wire connections since the tube that enters this region 
\item Use a dremmel with a fine tip to begin each of the drill sites. Be careful to stay within the trace lines drawn in the step above so that holes are not over-drilled. 
\end{enumerate}
\clearpage

\section{Avionics}
The following images show the wiring and organization of the main body of the Albatross UAV, before the addition of the battery. Note that hook and loop was used to secure the pixhawk and other components inside the fuselage. All the wiring is also tied off and organized for ease in making adjustments and testing individual components.\newline 

\begin{center}
 \newline


\end{center}

\subsection{Battery Care}
\subsection{Wiring and Soldering}
\subsection{Taranis}

\clearpage

\end{document}

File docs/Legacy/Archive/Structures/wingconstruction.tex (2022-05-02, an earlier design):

\documentclass{article}
\usepackage[margin=1in]{geometry}

\begin{document}

\title{\textbf{Wing Construction Outline}}
\author{Abigail Gries}
\maketitle

This is a step-by-step guide explaining how to construct the UAS wings out of foam. \\

\section*{Materials/Resources}

\begin{itemize}
	\item Large hot wire capable of reaching at least 12 volts
	\item Exacto knife
	\item Heavy weight
	\item EPP Foam (at least 6 ft x 1 ft x 2 in)
	\item Masking or duct tape
	\item Wood or metal (for airfoil template)
	\item Table or surface to work on 
	\item Nearby outlet
	\item Box fans
	\item Two 1/8th inch screws
	\item Tape measure
	\item Sharpie or pen

\end{itemize}

\section*{Procedure}
\begin{enumerate}
	\item Create a wooden or metal template of the NACA 4512 airfoil. Make sure the material can withstand high heats and has screw two screw holes.
	\item Measure out 2 ft 7 inches on the foam. Mark with a line across the foam.
	\item Measure out 6 inches on the foam (width). Mark with a line across the foam.
	\item Set up hotwire according to instructions. Make sure that the cord can reach entire distance while cutting. 
	\item Set up box fans and open doors so that fumes will exit the area while cutting.
	\item Lay foam on cutting surface and place a heavy weight on the top of the foam.
	\item Turn hotwire on to 12 volts.
	\item Cut foam long ways first - across the 2 ft 7 in line. The key is to go very slowly without stopping. Do not apply much pressure - let the hot wire do 					work for you.
	\item Turn hot wire off
	\item Let wire cool before wiping any foam residue off with paper towel

\end{enumerate}

\end{document}

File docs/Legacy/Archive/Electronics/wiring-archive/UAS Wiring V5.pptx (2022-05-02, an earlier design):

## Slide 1

Battery

PDB

ESC

Motor

BEC
(Backup system)

BEC (Servos)

Red – Power
Black – Ground
Yellow – Signal
Gray - Other

Pixhawk

Inductor

Aux Out

Main Out

*From motor’s ESC, only signal and ground are needed

Servos

Power

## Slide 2

Servo BEC

Servos

Motor ESC

Telemetry Radio Receiver

Main Out 1 – Right Aileron
Main Out 2 – Left Aileron
Main Out 3 – Right Elevator
Main Out 4 – Rudder
Main Out 5 – Throttle
Main Out 8 – Servo BEC 2
Aux Out 1 – Servo BEC 1
Aux Out 2 – Left Elevator

Tranceiver Set

Aux Out 1

Aux Out 2

Pixhawk

Aux Out 3

Aux Out 4

Aux Out 5

Aux Out 6

Main Out 1

Main Out 2

Main Out 3

Main Out 4

Main Out 5

Main Out 6

Main Out 7

Main Out 8

SBUS

RCIN

SPKT/DSM

Buzzer

Telem 2

Switch

Serial 4/5

Telem 1

GPS

GPS Module

AirSpeed sensor

USB

ADC 3.3 V

CAN

SPI

12C

CRIUS I2C Splitter

PDB

Power

ADC 6.6 V

## PDB

MAUCH Power Monitor
- Provides necessary power to the Pixhawk and the rest of the system
- Monitors battery power and sends information to the pixhawk

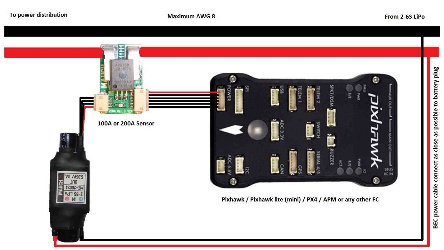
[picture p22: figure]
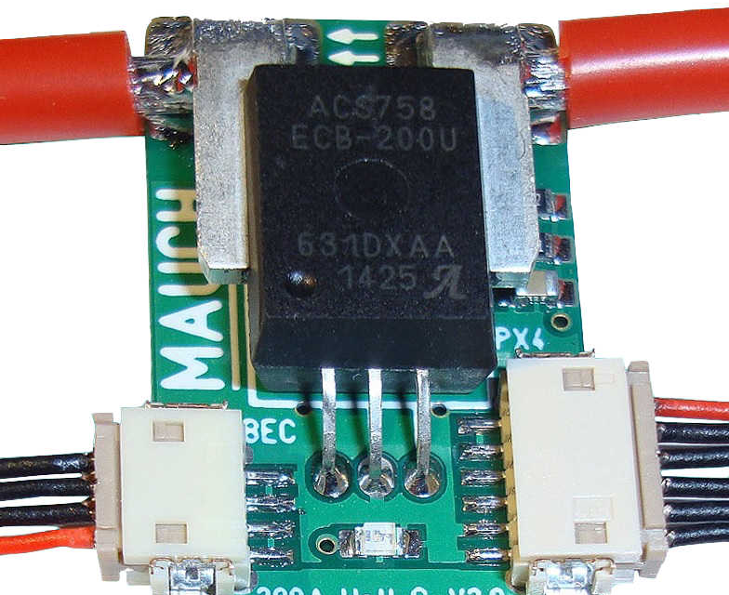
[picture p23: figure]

## BEC (Battery Elimination Circuit) (backup)

Mauch BEC
- Connected to the main 12 V line as close to battery as possible
- Drops voltage to 5 V and feeds into the PDB
- Used to drop voltage for pixhawk

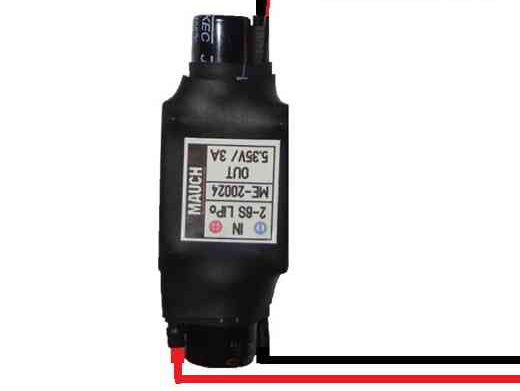
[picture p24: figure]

## BEC (Battery Elimination Circuit) (Servo)

Castle Creations CCBEC pro
- Connected to the main 12 V
- Drops voltage to 5 V and feeds into the both the Aux and Main servo Rails on the pixhawk
- Used to drop voltage to 5V to power the servos

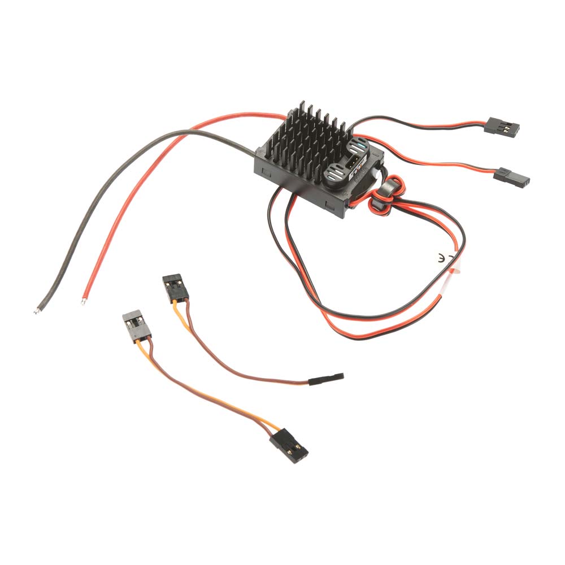
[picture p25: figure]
Image result for caslte creations ccbec pro

## ESC (Electronic Speed Controller)

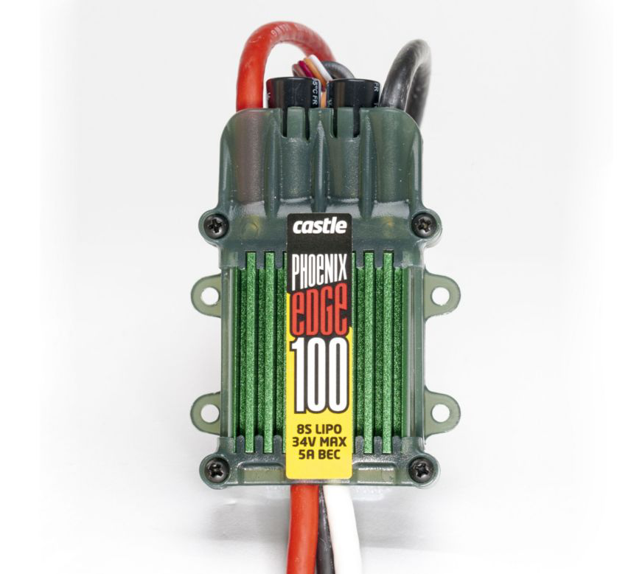
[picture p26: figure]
Image result for phoenix edge ESC 100 amp esc

Phoenix Edge
- Used to control the motor
- Powered via the 12 V line
- Takes PWM input from the Pixhawk main 5 channel
- PWM input line has an inductor

## Telemetry Radio Receiver

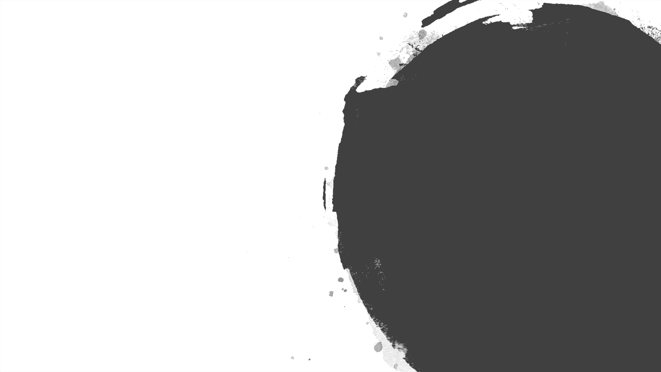
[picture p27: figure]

FrSky S8R 8/16ch Receiver
- Receives radio commands from the Taranus controller
- Sends commands to pixhawk via RCIN

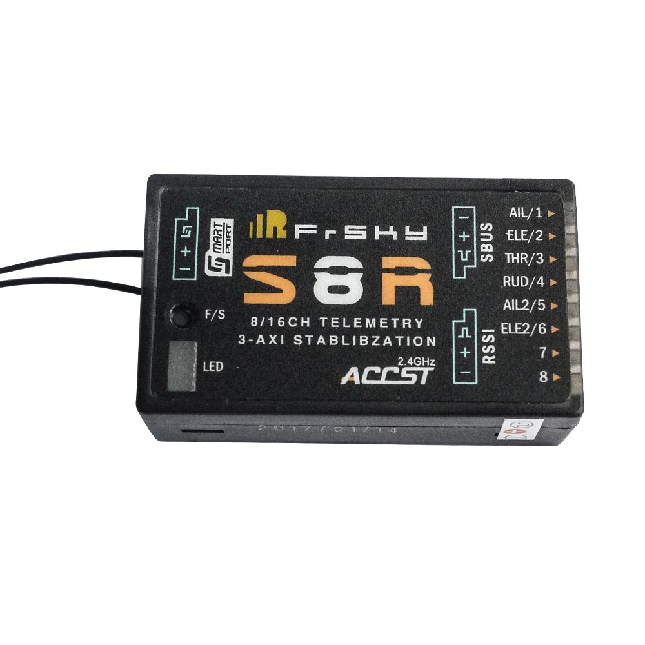
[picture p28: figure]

## Transceiver Radio set

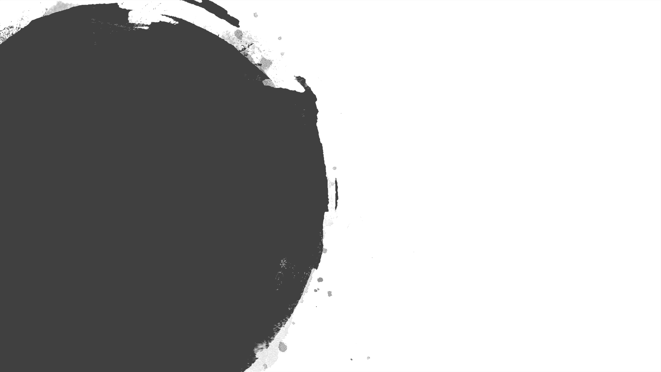
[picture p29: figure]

jD-RF900Plus Longrange
- Communicate between the pixhawk and the GroundStation
- The Fixed wing transceiver is plugged into the Telemetry 1 port
- The Ground station Transceiver is plugged into a computer via USB

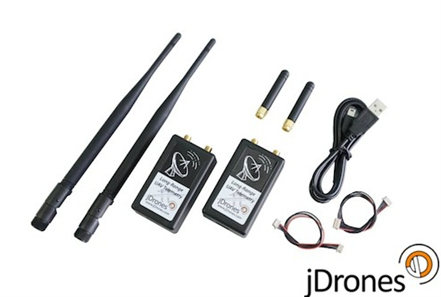
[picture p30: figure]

## GPS

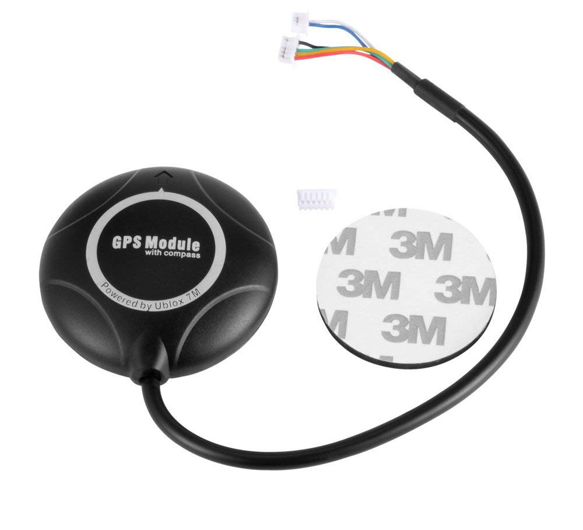
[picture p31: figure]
Image result for Ublox 7m gps module

- Provides GPS signal to pixhawk
- Cables go to I2C splitter & GPS port on the pixhawk

## Airspeed Sensor

MS5525 airspeed sensor
- Senses airspeed
- Connected to I2C port on the Pixhawk

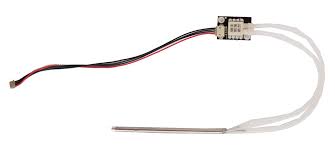
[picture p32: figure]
Image result for pixhawk airspeed sensor

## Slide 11

1. Cirius Pixhawk-i2c Splitter Expand Module for Pixhawk APM Flight Controller

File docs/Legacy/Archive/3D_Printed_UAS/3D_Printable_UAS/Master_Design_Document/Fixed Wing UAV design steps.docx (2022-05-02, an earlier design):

This is a description of the general procedure when designing a fixed wing UAS, as described by Giuseppe Landolfo in his thesis titled Aerodynamic and Structural Design of A Small Nonplanar Wing UAV. While most of this paper is about nonplanar wing design, I have found a lot of useful information in Chapter III Design Requirements and Chapter IV Aircraft Initial Sizing. I have taken a few screenshots of the REALLY useful tables and figures that I thought would be awesome information to use.

1. This method was designed for a fixed wing UAS with the following requirements:

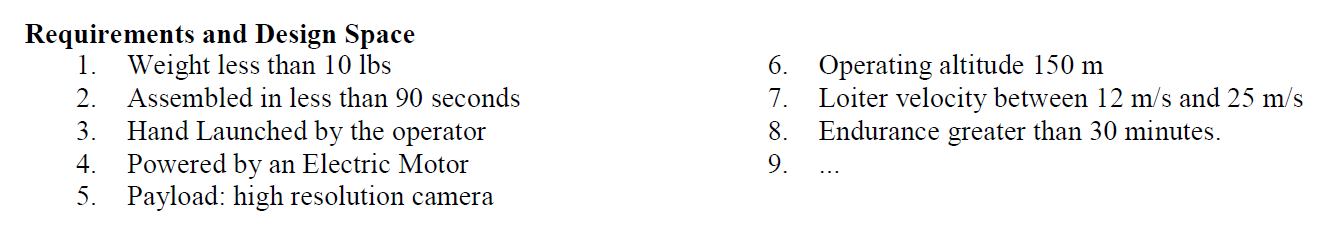
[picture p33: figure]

The table below shows a general outline of features for previous successful fixed wing UAS:

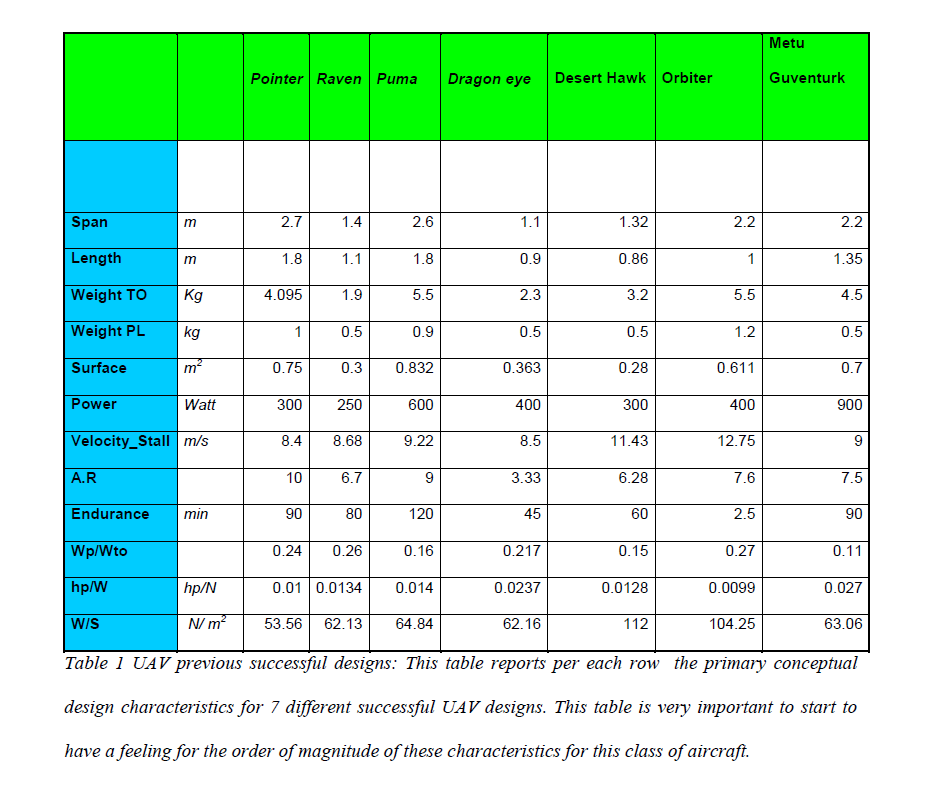
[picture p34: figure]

2. The first important step is to determine what the weight of your payload will be. This is where we will decide what sensors we believe are necessary for our UAS. Once we determine the weight of our sensors, parallela board and any other payload, we will know our approximate take-off weight. Below is a table which shows the payload weight fractions of previously successful UASs. It was found that the average Wp/Wto fell around 0.201.

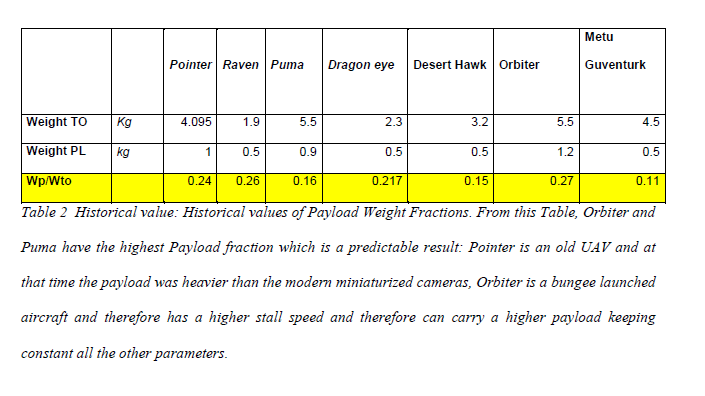
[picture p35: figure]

3. After determining the take-off weight, we will now pick a design point. Using the horsepower to weight ratio vs wing loading diagram below, we are able to see the general design space in which we can work with. By picking a design point, we are then able to determine what the surface area of our wing will be as well as the thrust available.

In general:

-An aircraft with a higher hp/W ratio will accelerate more quickly, climb more rapidly, reach a higher max speed, and sustain higher turn rates

-The Wing Loading (W/S) affects the stall speed, climb rates, takeoff/landing distances, turn performances, Cl and drag. A larger wing will typically have a low wing loading – this may improve the performance of the aircraft, but it will also increase drag. It is important to find a good compromise when it comes to wing loading.

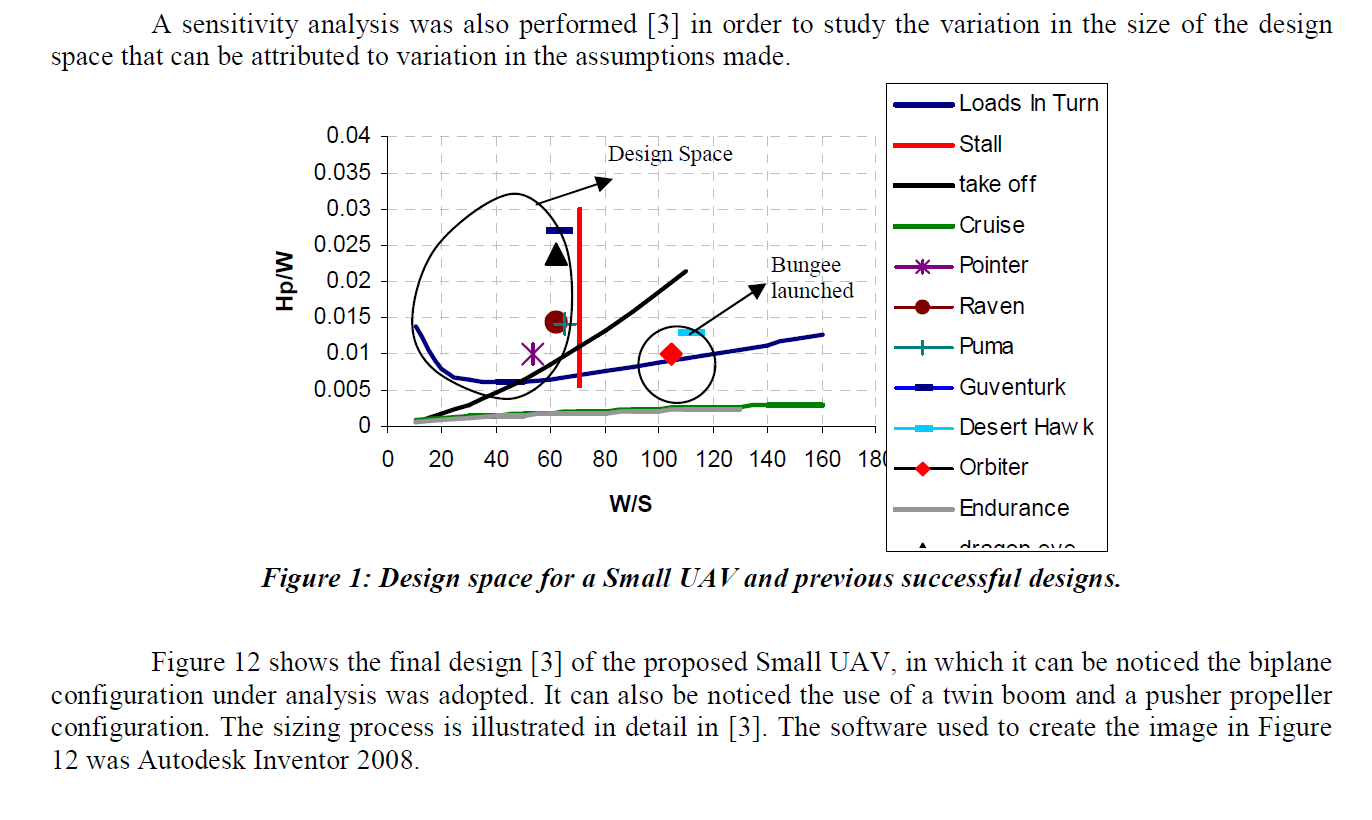
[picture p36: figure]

4. Once we have picked a design point, we have the capability to determine the wing geometry. We will determine the surface area of the wing by using the formula S=W/(W/S) since we know the weight of our aircraft as well as the wing loading. At this point we will pick an aspect ratio of our choice. I suggest that we use some of the tables to see what previous aircrafts have used in order to make an educated decision about what will work best for ours. Once the aspect ratio is decided, we can calculate the span and chords (very simple multiplication calculations which are shown in the paper).
5. At this point we can start determining some of the flight characteristics of our aircraft, and we can make an initial estimate of our operating lift coefficient, drag coefficient and lift to drag ratio. We can determine the operating lift coefficient by: C_L =W/(1/2ρV^2 S) where we have determined W/S, rho, and we can pick an arbitrary V cruising speed. From this point we will determine our first lift to drag ratio estimate by analyzing our airfoil as a flat plate (only for aspect ratio > 4. We know that the coefficient of lift is a function of the angle of attack defined by C_L =2πα . We also know the induced drag coefficient is defined by C_(Di) =(C_L^2)/(πeAR) . An assumption was made in the paper that the parasitic drag is approximately 0.03. Using these assumptions, we are able to draw a graph of the lift to drag ratio (L/D) as a function of the angle of attack. This allows us to determine our operating lift to drag ratio corresponding to our operating angle of attack (which is determined by the previously defined formula C_L =2πα at the operating lift coefficient found in the step above). The example of this step from the paper is shown below:

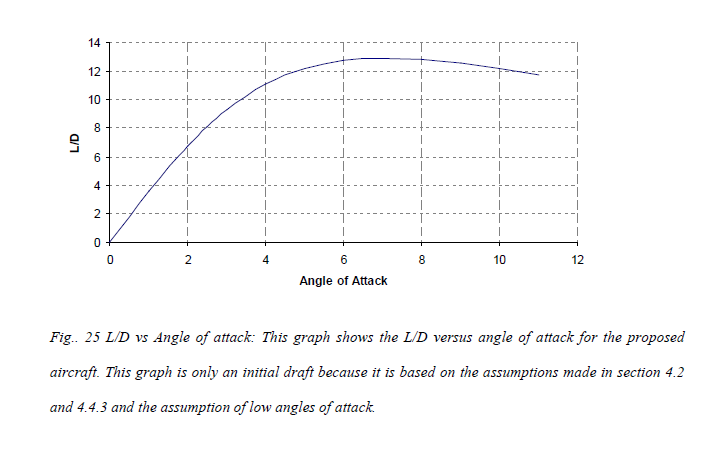
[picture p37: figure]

6. At this point we are able to start making decisions about the battery/motor combination. The graph below shows how the weight of the battery will have an effect on the thrust performance of the aircraft

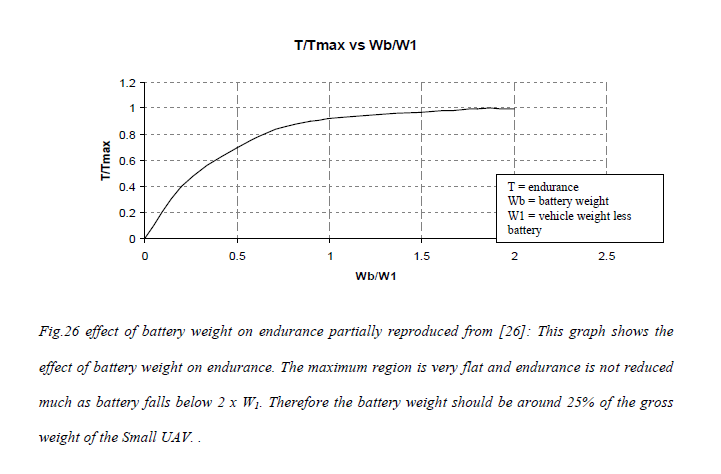
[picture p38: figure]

We can see that in order to achieve maximum performance, the battery should encompass approximately 25% of the weight of the UAS. In section 4.4.4.3 of the paper, there is a really good description which will help us calculate the power that will be required to operate our UAS at different angles of attack. We will decide the angle of attack that our UAS needs to be able to sustain which will give us the corresponding power requirement. Using this requirement, we will be able to make decisions about what size and kind of battery will be required in order to operate our UAS, as well as choose a propulsion system. Below is the example from the paper of what the power requirement is with respect to angle of attack:

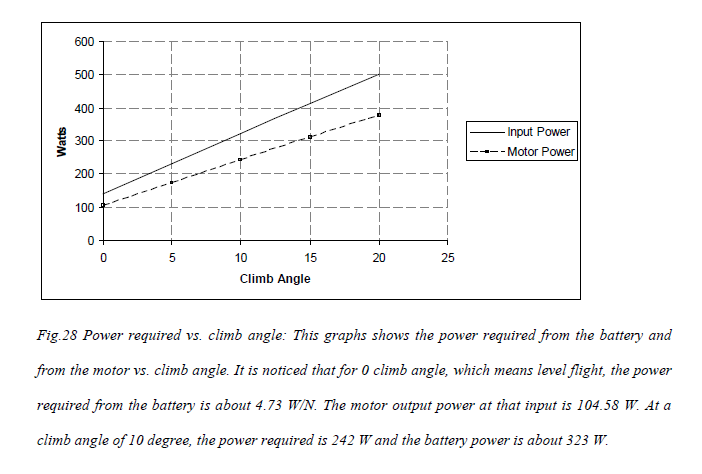
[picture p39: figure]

Raven/Pointer?!:

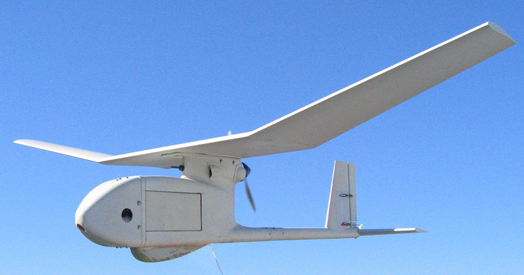
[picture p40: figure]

WASP

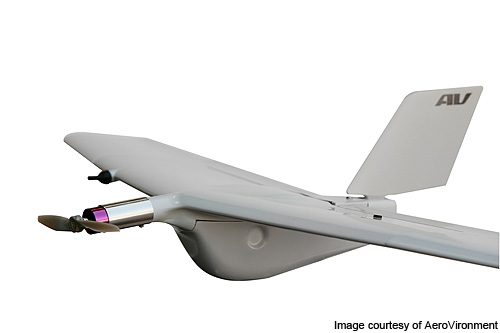
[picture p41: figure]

General characteristics

- Crew: none
- Length: 1.25 ft (38 cm)
- Wingspan (https://en.wikipedia.org/wiki/Wingspan): 2.375 ft (72.3 cm)
- Height: ()
- Empty weight (https://en.wikipedia.org/wiki/Manufacturer's_empty_weight): 0.95 lb (430 g (Land version))
- Loaded weight: 14.4 lbs (6.53 kg)
- Powerplant (https://en.wikipedia.org/wiki/Aircraft_engine): 1 × Electric motor, rechargeable lithium ion batteries, ()

Performance

- Maximum speed (https://en.wikipedia.org/wiki/V_speeds): 40mph 65 km/h
- Cruise speed (https://en.wikipedia.org/wiki/V_speeds): 40 - 65 km/h
- Range (https://en.wikipedia.org/wiki/Range_(aeronautics)): 5 km ()

PUMA

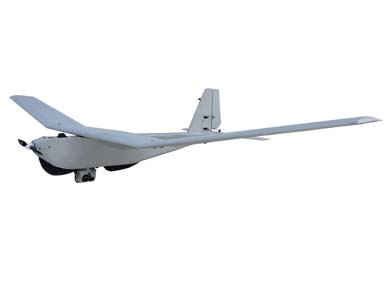
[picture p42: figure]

DESERT HAWK

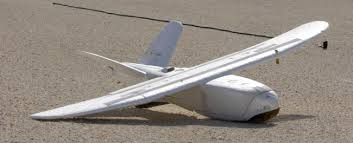
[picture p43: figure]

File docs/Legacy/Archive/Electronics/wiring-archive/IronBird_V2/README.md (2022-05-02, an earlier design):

Solidworks models for the components of the Iron Bird V2

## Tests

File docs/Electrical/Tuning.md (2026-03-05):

# PX-4 PID Tuning

This page talks about tuning the controller gains in PX-4. This is essential for pilots seeking certain flight characteristics, such as increased responsiveness to controller inputs.

We have been using the same guidelines as [PX-4's Tuning Guide](https://docs.px4.io/main/en/config_fw/pid_tuning_guide_fixedwing.html) and we recommend following the same process. Here we have added some more information and lessons learnt.

## Background 

In a UAS, a PID controller ensures that the UAS responds the way the pilot expects it to. A PID controller takes in the error signal in roll, pitch, or yaw (i.e. the difference between the pilot's input command and the actual behavior) and then performs some calculations so that the error is minimized.

The PID controller has gains, or constant multipliers, corresponding to three calculations:

*Proportional*: This gain is proportional to the error signal. Increasing the P gain will proportionally send a larger correcting signal if there is a large current error.

*Integral*: This gain is proportional to the *integral* of the error signal. Essentially, it corresponds to a large signal if the cumulative error is large.

*Derivative*: This gain is proportional to the derivative of the error. It contributes to a signal that is proportional to the instantaneous rate of change of error which it finds as the difference between the current and previous error.

## Pitch tuning process

Pitch tuning focuses on adjusting the controller gains so that the aircraft responds smoothly and accurately to pitch commands. The process typically begins by tuning the **proportional (P) gain**, which determines how strongly the controller reacts to a pitch error. Increasing the P gain makes the aircraft respond faster to pitch commands such as climbs or descents. However, if the gain becomes too high, the aircraft may begin to oscillate in pitch, so the value should be increased gradually until the response is quick but still stable.

After the P gain is set, the **derivative (D) gain** can be adjusted to help damp oscillations and reduce overshoot when the aircraft approaches the desired pitch angle. Finally, a small **integral (I) gain** can be introduced to correct steady-state errors, such as the aircraft slowly drifting away from the commanded pitch attitude. The integral term accumulates small errors over time and helps the aircraft maintain the desired pitch angle during steady flight.

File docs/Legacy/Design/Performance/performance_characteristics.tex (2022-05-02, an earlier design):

\documentclass{article}
\usepackage[margin=1in]{geometry}
\usepackage{amsmath}
\usepackage{graphicx}

\begin{document}

%Command to change name of table of contents
\renewcommand*\contentsname{Table of Contents}

%Command to start sections on new pages
\newcommand{\sectionbreak}{\clearpage}

\title{\textbf{Performance and Design Calculations}}
\author{Abigail Gries}
\maketitle

This document shows how to calculate important design and performance characteristics of a UAS. 

\newpage

\tableofcontents

\newpage

\section{Variable Definitions}

\begin{itemize}
\item \textit{AR} - The aspect ratio \\
\item \textit{e} - The Oswald Efficiency factor\\
\item $\bar{c}$ - The mean chord length of a wing\\
\item \textit{K} = Wave drag due to lift \\
\item \textit{a} = Slope of $C_L vs \alpha$ \\
\item $C_L$ = Coefficient of lift for a given angle of attack \\
\item $C_{Di}$ = Coefficient of induced drag\\
\item ${C_{D,0}}$ = Coefficient of zero-lift drag\\
\item $C_{fe}$ = Skin friction coefficient\\
\item $S_{wet}$ = Total wetted surface of UAV\\
\item $E_M$ = Maximum aerodynamic efficiency \\
\item \textit{Re} = The Reynolds number\\
\item \textit{Rt} = Battery hour rating\\
\item \textit{n} = Battery discharge parameter\\
\item \textit{V} = Battery voltage\\
\item \textit{C} = Battery capacity\\
\end{itemize}

\newpage

\section{Wing Design}

When designing a wing, the typical first step is to determine the required wingspan, wing planform area, and main airfoil. Additionally, based on the intended flight goals, a taper ratio and sweep angle of the wing also should be chosen. From these preliminary values, the performance of the wing can be calculated. The wing parameters are arguably some of the most influential characteristics on the overall performance of the UAV. \\

\noindent The OpenUAS team has chosen the following preliminary wing characteristics based on the requirements and the intended flight goals. The airfoil selected is NACA 4512 (see Fig. 1 below or Airfoil Documentation). \\

\begin{figure}[ht]
\begin{center}
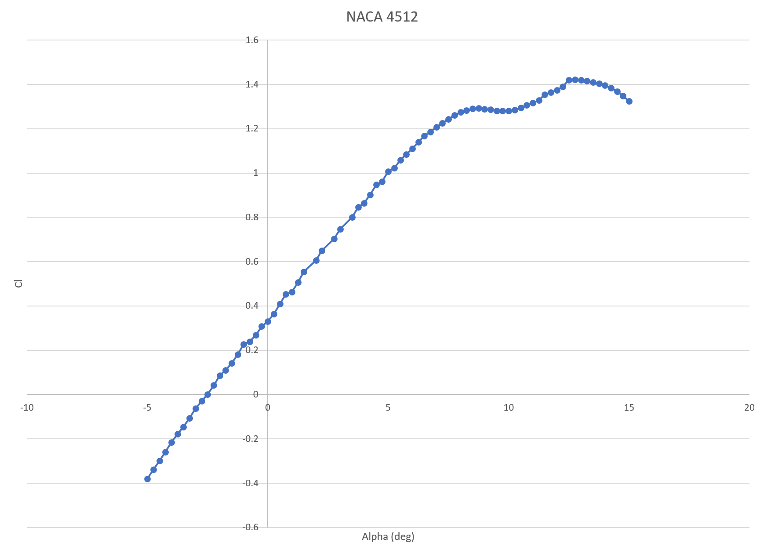
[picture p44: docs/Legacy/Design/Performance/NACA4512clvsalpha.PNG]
	
	\caption{NACA 4512 $Cl$ vs $\alpha$}
	\label{Figure 1:}

\end{center}
\end{figure}

\begin{center}
\begin{tabular}[pos]{| c | c | c | c | }
\hline
\textbf{Variable} & \textbf{Description} & \textbf{Value} & \textbf{Units} \\ \hline
\textit{b} & Wingspan & 5 & $ft$ \\ \hline
\textit{S} & Wing Area & 2 & $ft^2$ \\ \hline
$\tau$ & Taper Ratio & 0 & \\ \hline
$\Lambda$ & Sweep Angle & 0 & \textit{degrees} \\ \hline
\textit{$a_0$} & Slope of $C_l$ vs $\alpha$ & 0.134 & \\ \hline
$\alpha_{L=0}$ & Zero Lift Angle of Attack & -2.3 & $degrees$ \\ \hline
\end{tabular} \\~\\
\end{center}

\newpage
\section{Aerodynamics}

Equation 1 demonstrates how to calculate the aspect ratio of a wing. As the aspect ratio of a wing increases, the aerodynamic efficiency of a wing increases as well [1]. The OpenUAS will have a high aspect ratio because the design is almost glider-like. \\
\begin{equation}
AR = \frac{b^2}{S}
\end{equation}
As the true OpenUAS wing is 3D and not an ideal, a correction factor must be applied to certain wing calculations. This correction factor is the Oswald Efficiency factor shown in equation 2 below. \\
\begin{equation}
e =1.78(1-0.45AR^{0.68}) - 0.64
\end{equation}
Equation 3 demonstrates how to calculate the (standard) mean chord length of the wing. 
\begin{equation}
\bar{c} = \frac{S}{b}
\end{equation}
The equation below shows how to calculate $K$, the wave drag due to lift. This value is very useful in estimating important characteristics of the aircraft, such as induced drag, maximum aerodynamic efficiency, and lift of a wing. 
\begin{equation}
K = \frac{1}{\pi eAR}
\end{equation}
Figure 1 above shows the $Cl$ vs $\alpha$ plot for the main airfoil. The slope of the linear line on this plot is $a_0$ and is used to described the selected airfoil. The slope for the wing, $a$ is calculated in equation below. $a_0$ cannot be used in the place of $a$ because the wing is 3D and features of the wing affect the coefficient of the lift produced, thus changing the slope.\\
\begin{equation}
a = \frac{a_0cos(\lambda)}{1+Ka_0cos(\lambda)}
\end{equation}
Using the $a$ value calculated above, the coefficient of lift calculated at any angle of attack can be found with equation 6. \\
\begin{equation}
C_L = a(\alpha - \alpha_{L=0})
\end{equation}
The coefficient of induced drag, or drag due to lift, is estimated using the $K$ and $C_L$ values obtained above. \\
\begin{equation}
C_{Di} = KC_L^2
\end{equation}
The coefficient of zero lift drag is the drag when the lift of an aircraft is equal to zero. This is based on the shape of the aircraft.
\begin{equation}
{C_{D,0}} = C_{fe}\frac{S_{wet}}{S}
\end{equation}
The maximum aerodynamic efficiency describes the best case scenerio lift to drag ratio of an aircraft.
\begin{equation}
E_M = \frac{1}{2\sqrt{KC_{D,0}}}
\end{equation}
\begin{equation}
Re = \frac{\rho v\bar{c}}{\mu}
\end{equation}

\newpage
\section{Take-Off}

\newpage
\section{Climb}

\newpage
\section{Cruise}

\newpage
\section{Landing} 

\newpage
\section{References}

\end{document}

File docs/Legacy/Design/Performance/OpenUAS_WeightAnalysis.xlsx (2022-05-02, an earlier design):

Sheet: airplane
 |  | kg | Newtons | lb |  |  | Output
 | Convert | 2.72 | 26.674088 | 6.00 |  |  | Battery weight fractions | Battery weight fractions |  | battery weight
 |  |  |  |  |  |  | Take-off | 0.00036 |  | 0.03735 | N
g | 9.8 | m/sec^2 |  |  |  |  | Best range cruise | 0.23872 |  | 24.45317 | N
airplane |  |  |  |  |  |  | Loiter | 0.00000 |  | 0.00000 | N
aspect ratio | 8.57 |  |  |  |  |  | Cruise | 0.25353 |  | 25.97012 | N
CDo | 0.025 |  | 0.48 |  |  |  | Turns | 0.00000 |  | 0.00000 | N
span efficiency (e) | 0.795
propeller efficiency | 0.6
motor efficiency | 0.8 |  |  |  |  |  | total Wb/Wto | 0.49261 |  | 50.46065 | N
W/S wing loading (S) | 98.71 | N/m^2 | 32.985623 | oz/ft^2 | 2.061601437 | lbs/ft^2
P/W power loading (W/N=m) | 10 | W/N or (m/sec) | 44.48220489 | watts/lb | 2.780137806 | watts/oz | Wto | 102.43 | N | 10.44544 | kg | 23.02817908 | lb
k_battery | 48317.6204 | J/N or (m) | 215703.66 | J/lb |  |  | Wempty | 40.97 | N | 4.17818 | kg | 9.211271633 | lb
We/Wto empty weight fraction | 0.4 |  |  |  |  |  | Wbattery | 50.46 | N | 5.14557 | kg | 11.34400845 | lb
payload weight (N) | 11 | N | 2.47 | lb
 |  |  |  |  |  |  | S wing area | 1.04 | m^2 | 11.17004 | sq. ft
k Drag due to lift factor | 0.04671992928 |  | k=1/(pi*ar*e) |  |  |  | b wing span | 2.98 | m | 9.78403 | ft
(L/D) max (emax) | 14.63015447 |  | 1/(2*sqrt(k*cdo)) |  |  |  | Power | 1024.34 | Watts
Density of air | 1.1117 | kg/m^3
CLmax | 1.4 |  |  |  |  | to
 |  |  |  |  |  | 8
For Thunderpower 5S 5000 mAh | W (N) | E_batt (W-hr) | E_batt (J) | k_batt
www.thunderpowerrc.com/air_batteries/5000-mAhE/TP5000-4SE55 | 4.9621649 | 74 | 266400 | 53686.24489

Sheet: take off
Take off |  |  |  |  |  |  |  |  | velocity conversions from m/sec
 |  |  |  |  |  |  |  |  | 3.280839895 | ft/sec
Density of air | 1.225 | kg/m^3 |  |  |  |  |  |  | 1.943844492 | knots
Clmax | 1.4
Take off velocity | 12.87492648 | m/sec | 42.24057243 | ft/sec | 25.02685492 | knots | 28.80039029 | miles/hr | 2.236936292 | miles/hour
time for take off | 1.761944428 | sec
take off distance | 15.12326998 | m
Wb/Wto for take off | 0.0003646587753
stall velocity | 10.7291054 | m/sec | 35.20047702 | ft/sec | 20.85571244 | knots | 24.00032524 | miles/hr
 |  |  |  | vlo=1.2*sqrt(2*wos/(sigma*rho_sl*Clmax)); % Take-off Velocity [Brandt Eq.5.52, Pg.221]
 |  |  |  | t_takeoff=0.7*(vlo)^2/(g*PoW*eta_p*eta_m);
 |  |  |  | s_takeoff=1/3*(vlo)^3/(g*eta_p*eta_m*PoW);
 |  |  |  | wb_wto=t_takeoff*PoW1/k_batt % Battery Weight / Take off weight

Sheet: Best range cruise
Cruise 1 |  |  |  |  |  |  |  |  | velocity conversions from m/sec
Density of air | 1.225 | kg/m^3 |  |  |  |  |  |  | 3.280839895 | ft/sec
cruise distance | 81 | km |  |  |  |  |  |  | 1.943844492 | knots
Time | 1.515878686 | hrs
Cruise velocity | 14.84287642 | m/sec | 48.6971011 | ft/sec | 28.85224357 | knots | 33.20256893 | miles/hr | 2.236936292 | miles/hour
Cruise time | 5457.16327 | sec | 90.95272117 | min
q- dynamic pressure | 134.9404754 | N/m^2
L/D at cruise velocity | 14.63015447
Wb/Wto for cruise | 0.2387202894
 |  |  |  | LoD= wos/(cdo*q+k*(wos^2)/q) % Lift over Drag

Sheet: loiter
Loiter/Arrival |  |  |  |  |  |  |  |  | velocity conversions from m/sec
Density of air | 1.225 | kg/m^3 |  |  |  |  |  |  | 3.280839895 | ft/sec
Loiter distance | 0 | km |  |  |  |  |  |  | 1.943844492 | knots
time | 0 | hrs
Loiter velocity | 11 | m/sec | 36.08923885 | ft/sec | 21.38228942 | knots | 24.60629921 | miles/hr | 2.236936292 | miles/hour
Loiter time | 0 | sec | 0 | min
q- dynamic pressure | 74.1125 | N/m^2
L/D at Loiter | 12.34624929 |  |  |  |  | LoD= wos/(cdo*q+k*(wos^2)/q) % Lift over Drag
Wb/Wto for cruise | 0 |  |  |  |  | wb_wto=x/(eta_p*eta_m*k_batt*LoD) % Battery Weight / Take off weight

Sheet: Cruise
Cruise-dash |  |  |  |  |  |  |  |  | velocity conversions from m/sec
Density of air | 1.225 | kg/m^3 |  |  |  |  |  |  | 3.280839895 | ft/sec
cruise distance | 80 | km |  |  |  |  |  |  | 1.943844492 | knots
time | 1.234567901
Cruise velocity | 18 | m/sec | 59.05511811 | ft/sec | 34.98920086 | knots | 40.26485326 | miles/hr | 2.236936292 | miles/hour
Cruise time | 4444.444444 | sec | 74.07407407 | min
q- dynamic pressure | 198.45 | N/m^2
L/D at cruise velocity | 13.60551875 |  |  |  |  | LoD= wos/(cdo*q+k*(wos^2)/q) % Lift over Drag
Wb/Wto for cruise | 0.2535292706 |  |  |  |  | wb_wto=x/(eta_p*eta_m*k_batt*LoD) % Battery Weight / Take off weight

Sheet: Turns
 |  |  |  |  |  |  |  |  | velocity conversions from m/sec
theta | 0 |  |  |  |  |  |  |  | 3.280839895 | ft/sec
air density | 1 | kg/m^3 |  |  |  |  |  |  | 1.943844492 | knots
Turn Velocity | 14.24993233 | m/s | 46.75174649 | ft/sec | 27.69965248 | knots | 31.87619079 | miles/hr | 2.236936292 | miles/hour
dynamic pressure | 101.5302857 | N/m^2
load factor n | 2.617198598
Wb/Wto for sustained turn | 0

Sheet: landing
landing
approach velocity | 12.87492648 | m/s
density of air | 1.1117 | kg/m^3
mu - braking coefficient | 0.5
beta - weight fraction | 1
Clmax landing | 1.3
W/S wing loading | 98.71 | N/m^2
landing field length | 23.54503261 | m

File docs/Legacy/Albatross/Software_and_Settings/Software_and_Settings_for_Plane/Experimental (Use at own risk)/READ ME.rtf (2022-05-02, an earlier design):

This folder represents settings and software that is not tested and while may be operational, a high level of risk is present but also provides the most cutting edge software and settings. Use at your own risk.

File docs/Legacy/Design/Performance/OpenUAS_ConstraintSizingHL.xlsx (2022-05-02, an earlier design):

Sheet: airplane
 |  | kg | Newtons | lb
 | Convert | 20 | 196.133 | 44.09
Airplane
g | 9.8 | m/sec^2
airplane
aspect ratio | 8.57
Cdo | 0.025
span efficiency (e) | 0.8
propeller efficiency | 0.6
motor efficiency | 0.8
k Drag due to lift factor | 0.04642792972 |  | k=1/(pi*ar*e)
(L/D) max (emax) | 14.67608914 |  | 1/(2*sqrt(k*cdo))
Hand Launch
CLmax | 1.2
Vthrow | 7.5 | m/s | 24.6 | ft/s
Maximum Speed
Altitude | 100 | m |  |  |  |  | 67.10808876 | miles/hr
velocity | 30 | m/sec | 98.42519685 | ft/sec | 67.10808876 | mph
q | 546.6852494 | N/m^2
Density of air | 1.21485611 | kg/m^3
Landing
Altitude (landing) | 0
CLMax | 1 | (from takeoff)
Landing Distance | 10 | m
Reverse Force Fraction | 0
Density at Altitude | 1.226571219 | kg/m^3
Thrust | 1 | Not used for electric |  | Used to correct the thrust for altitude
Rho Sea Level | 1.225 |  |  |  |  |  |  |  |  |  |  |  | English 2nd axis
 |  |  |  |  |  |  |  | Vapproach |  |  |  |  | 40 | 0.83 | lbs/sqft
Ceiling |  | c |  |  |  |  |  | Altitude | 100 | m |  |  | 100 | 2.09 | lbs/sqft
Altitude | 1900 | m | 6232 | ft |  |  |  | CLMax | 1.4 | ~
Density | 1.018236998 | kg/m^3 |  |  |  |  |  | Vapp | 9 | m/s | 29.52 | fps | 0 | 0 | W/lb
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

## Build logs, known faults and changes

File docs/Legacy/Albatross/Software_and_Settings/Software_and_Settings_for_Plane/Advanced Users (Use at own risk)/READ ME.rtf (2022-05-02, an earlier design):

This folder represents settings and software that is tested and operational but not to the extent that we warrant its’ ability. Use at your own risk.

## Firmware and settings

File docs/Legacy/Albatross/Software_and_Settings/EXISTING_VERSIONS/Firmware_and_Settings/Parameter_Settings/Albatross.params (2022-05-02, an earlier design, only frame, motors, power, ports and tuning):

1	1	BAT_CAPACITY	14000	9
1	1	BAT_C_SCALING	-1.000	9
1	1	BAT_N_CELLS	6	6
1	1	BAT_V_CHARGED	4.20	9
1	1	BAT_V_EMPTY	3.40	9
1	1	BAT_V_LOAD_DROP	0.07	9
1	1	BAT_V_SCALE_IO	10000	6
1	1	BAT_V_SCALING	-1.000	9
1	1	PWM_MAIN_REV1	0	6
1	1	PWM_MAIN_REV2	0	6
1	1	PWM_MAIN_REV3	0	6
1	1	PWM_MAIN_REV4	0	6
1	1	PWM_MAIN_REV5	0	6
1	1	PWM_MAIN_REV6	1	6
1	1	PWM_MAIN_REV7	0	6
1	1	PWM_MAIN_REV8	0	6
1	1	SYS_AUTOSTART	2106	6

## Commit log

2022-05-02 Imported docs from openUAS repo
    [AA Long Range Lidar.params, AA Short Range Lidar.params, Albatross.params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]
2022-05-03 Renamed intro and legacy folder
    [AA Long Range Lidar.params, AA Short Range Lidar.params, Albatross.params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]
2022-05-03 Added git LFS
    [BEC (to Pixhawk from Power Module).SLDPRT, BEC (used for Servos).SLDPRT, BEC.SLDPRT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]
2022-05-24 Created all category readme's and added medium-zoom plugin for wiring diagram
    [openuas-electronics.dsn]
2022-09-24 Added parameters, battery charger manual, and pixhawk 4 pinout, need to embed pdf into page
2023-04-18 Updating Poster Board Arrangement page
2023-04-18 Fixing the bugs in Poster Board page
2023-04-18 Adding poster board image
2025-06-08 PLUMA Wiring Diagram
2026-03-04 Update wiring diagram image in README
2026-03-05 Updated the pitch tuning process
2026-04-22 Rename Wiring Diagram 2 (1).png to Wiring openuas5.png
    Change to make more sense
2026-04-22 Rename Wiring openuas5.png to Wiring-openuas5.png
    Changed the image name for my convience
2026-04-22 Update README.md
    Changed the wiring diagram order and updated to reflect the new Pixhawk usuage in the next 2 designs
2026-04-22 Update Components.md
    Added wiring diagram to the Git for components
